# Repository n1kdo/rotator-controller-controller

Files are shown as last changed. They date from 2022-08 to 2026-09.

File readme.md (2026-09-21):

# Raspberry Pi Pico W IOT Antenna Rotator Controller Controller

This project uses a Raspberry Pi Pico W to internet-enable an antenna 
rotator controller that has an RS-232 interface.  The software presents a web interface 
to the rotator, and also allows direct network control by N1MM+ and other software.

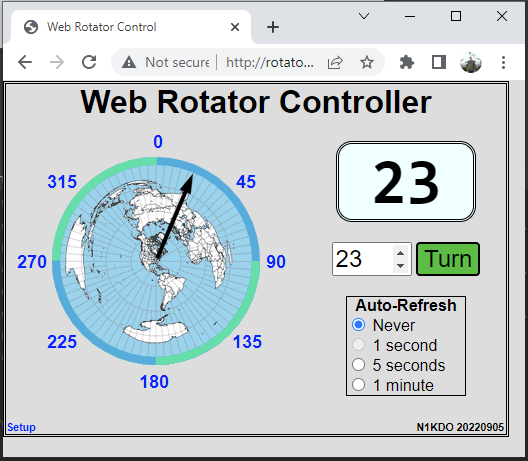
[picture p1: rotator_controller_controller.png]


I used it for my Hy-Gain Ham IV rotator.  My Hy-Gain rotator control box has been modified to allow computer
control with the addition of a Ham Supply/Idiom Press *Rotor-EZ* module.  I further modified the rotator
control box to provide +5 Volts on Pin 1 (carrier detect) of the DE-9S RS-232 interface.  This allows the 
Raspberry Pi Pico W to rob power from the rotator control box.

See the [Documentation](documentation.md) for details.

There is very little external hardware required.  The most important other piece is a MAX3232 3.3 volt 
RS-232 level converter.  The MAX3232 is used to interface the 3.3 volt logic of the Raspberry Pi Pico W to
the RS-232 levels required by the antenna rotator control box.

## Installing MicroPython on your Pico-W

1. Download the latest stable build of [Pico W MicroPython](https://micropython.org/download/RPI_PICO_W/). 
   [This is the direct link](https://www.micropython.org/resources/firmware/RPI_PICO_W-20260824-v1.29.0.uf2).
2. Connect a micro-USB cable to your PC.  Hold down the white "BOOTSEL" button on the Pico-W, and insert the
   micro-USB cable into your Pico-W.
3. The Pico-W should appear as a USB storage device on your computer.  On mine, it shows up as "RPI-RP2 (F:)".
4. Copy/Paste the MicroPython .uf2 file to this drive.
5. Disconnect the Pico-W and prepare for the next step.

## Installing this software onto the Pico-W

The easiest way to get this software installed onto your Pico-W is to use the `loader.py` tool, also
provided in this repository.

1. Download Python 3 from https://www.python.org/downloads/ and install it.  Make sure to select "Add 
   Python 3 to Path."
2. Download the contents of this GitHub repository as a zip.  Use this URL: 
   `https://github.com/n1kdo/rotator-controller-controller/archive/refs/heads/master.zip`
3. Unpack that zip file somewhere. 
4. Open a command prompt.  (your choice.  Could be PowerShell, could be good ole CMD.)
5. From the command line, execute the following command: `pip install pyserial` -- this will install the Python 
   serial port support/
6. Change directory to where you unpacked the GitHub zip file, and then
   change directory to the `src/loader` directory.
7. From the command line, execute the following command: `python loader.py` -- this will install all the rotator
   controller-controller software onto the Pico-W.

If you want to experiment, you can use the open-source "Thonny" IDE to load the python source code and HTML files
onto the Pico W.  Unfortunately, Thonny cannot load the binary file `compass-background.png` image file into the
proper location, but this can be worked around by using the "upload" feature in the controller-controller software.

## What is all this stuff?

Important files:

* src/rotator/main.py -- the main Python application
* src/rotator/dcu1_rotator.py -- a Python module that queries and commands the rotator controller
* src/rotator/http_server.py -- a Python module that implements the web server
* src/rotator/morse_code.py -- a Python module that implements the morse code sender
* src/rotator/n1mm_udp.py -- a Python module that implements UDP send/receive to/from N1MM+
* src/rotator/content/rotator.html -- the rotator control web page
* src/rotator/content/setup.html -- the setup web page
* src/rotator/content/files.html -- the file upload/download web page
* src/rotator/data/config.json -- the configuration file.  automatically generated on first use if not present.

Other Stuff:

* src/loader/loader.py -- small Python application installs the six files above onto the Pico-W
* src/loader/pyboard.py -- patched pyboard library from Micropython. Patched to work on Pico-W.

Electronic Design Files:

* kicad/* -- Kicad 6 design files for schematic and PCB.

## Other projects using this technology

I used this same electronic design, and a lot of the same source code to make
the [KPA-500 IOT Thing](https://github.com/n1kdo/KPA500-remote), a web interface and 
KPA500-remote *host* for the Elecraft KPA-500 amplifier.

## Yes it works with N1MM+

See [Using the Rotator Controller-Controller with N1MM+](N1MM.md)

n1kdo 2026-09-21

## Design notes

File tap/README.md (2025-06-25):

# Diagnostic/Development tools.

I built some tools to examine the data communications between apps and rotators while building this.

The tools are:

## line_tap.py

line_tap.py listens to serial data, both transmit and receive, using two additional serial ports.

It uses a "custom" tap to sense the transmit and receive lines on the RS-232 interface, and it sends
that data to the two ports described above.

I used this to listen in on serial traffic to and from the rotor control box (amongh other things.)

The harware tap has proven very useful for reverse-engineering serial protocols.

### Serial tap for reverse engineering

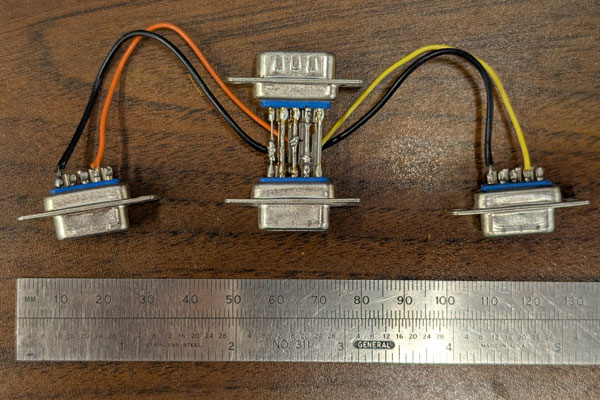
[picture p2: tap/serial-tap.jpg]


#### Serial Tap Wiring.

All pins are wired through from the device under test (DUT) _plug_ to the 
host socket.  Ground (pin 5) is wired to both the RX Tap and TX Tap grounds.  DUT TX
is wired to the TX Tap RX, and Host RX is wired to the RX Tap RX line.  The `line_tap.py`
script displays data from both paths.

| Pin | DE-9S Host | DE-9P DUT | DE-9P RX Tap | DE-9P TX Tap |
|-----|---|---|---|---|
| 1 | 1 | 1 | | |
| 2 | 2 | 2 | 2 | |
| 3 | 3 | 3 | | 2 |
| 4 | 4 | 4 | | |
| 5 | 5 | 5 | 5 | 5 |
| 6 | 6 | 6 | | |
| 7 | 7 | 7 | | |
| 8 | 8 | 8 | | |
| 9 | 9 | 9 | | |

# udp_listener.py

This script sends and receives Rotator control UDP messages to/from N1MM+

n1kdo 20250625

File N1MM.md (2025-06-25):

# Using the Rotator Controller-Controller with N1MM+

The rotator controller-controller software supports UDP messages in order that 
the connected rotator can be controlled with N1MM+.  You don't need any wires 
other than what connects the logging computer to the rotator controller-controller.

## Setup

Check the `N1MM Broadcasts` box, and make sure you have a unique `hostname` set.

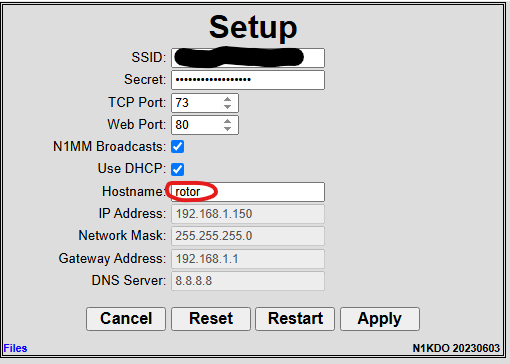
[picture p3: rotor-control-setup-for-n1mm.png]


## N1MM+ Setup

On the N1MM+ _configurator_ dialog, in the _Antennas_ tab, create an entry for an antenna,
specify the bands of that antenna, and make sure to use the _hostname_ specified above as the 
"Rotor Description."  The name must match exactly.

**Do not check** the "Start N1MM Rotor Program" -- you don't need it, you won't be using it.

Check one or both of the "Display Rotors" options.  The "...Responding from Network" option
will show all rotors that are reachable on the network; this will show you where the rotor(s)
are pointed _whether your station is using them or not._

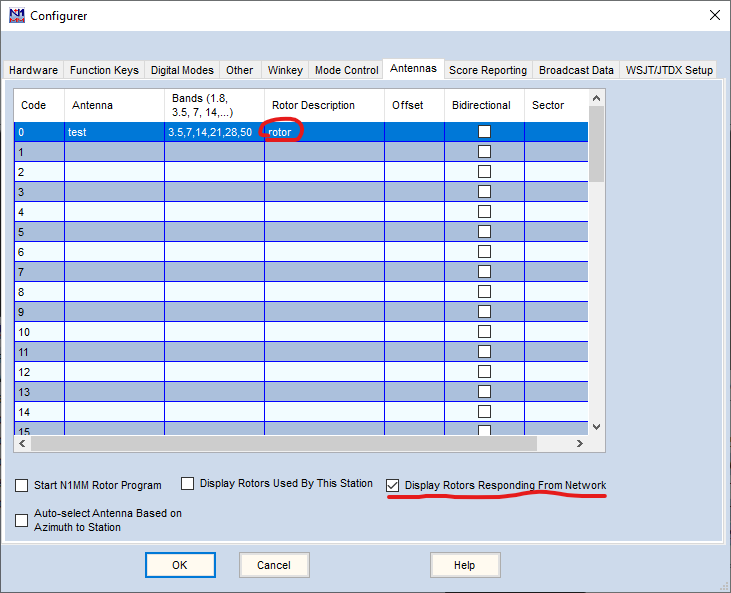
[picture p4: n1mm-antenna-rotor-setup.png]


## Operating

You should see a small window that shows the bearing of each configured rotor.  You will see the
rotor name/host name in the title bar of that window.



You can "move" the rotor by typing a bearing into the N1MM logger callsign box and pressing Alt-J.
This should turn the rotor to the new bearing.

N1MM has other tricks to turn a configured rotor; those are beyond the scope of this document.

---

n1kdo 2025-06-25

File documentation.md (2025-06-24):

# A Wireless Rotator Controller-Controller

Or: _How to Add Internet-of-Things Capabilities to Legacy Products_   
Jeff Otterson, N1KDO

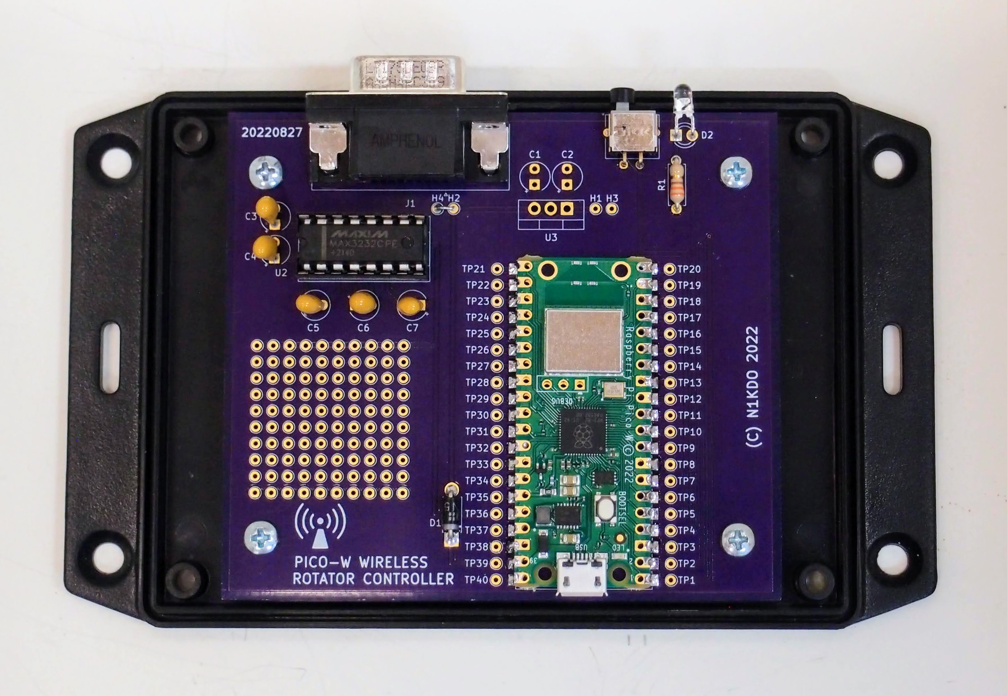
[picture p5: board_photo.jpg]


## Introduction

I live in a HOA neighborhood, which means no towers, no permanently installed visible antennas. For several years I have
been using a small 3-element Yagi which I temporarily erect on a tripod mount on my back patio for the May-August
6-meter Es season. This works well, but I have grown tired of “Armstrong”-style rotation of this antenna. I wanted to
use my Ham-IV antenna rotator to turn this antenna but did not want to go to the trouble of installing—and 
lightning-protecting the wiring for the rotator. Instead, I decided to find an approach to inexpensively add wireless 
control to the antenna rotator.

The first step was to modify the Ham-IV control box to add a computer interface. I bought the “Rotor-EZ” kit from
HamSupply (note 1) and installed it, to add RS-232 serial communications support to the Ham-IV. The Rotor-EZ uses the
same protocol as the HyGain DCU-3 and several other rotator controllers. This got me closer to my goal, but RS-232 still
needs wires!

In June 2022, the Raspberry Pi foundation announced their new “Raspberry Pi Pico-W” (note 2) – when I saw this new part,
I realized it was “just what the doctor ordered” for my project. I bought a few and started experimenting.

This article describes the results of my work: a wireless rotator controller-controller. The project connects the
rotator controller to your Wi-Fi network and allows both web-based and computer access to the rotator over wireless. The
approach I present here is useful for other Amateur Radio Internet-of-Things projects; I already have plans to use this
as a basis for wireless control of a remote antenna switch.

## How it works

If you look at the [schematic diagram](schematic.pdf), you will notice that there are very few electronic components.
Most of the components are used in the RS-232 level conversion. Like most everything else, this project is mostly in the
software.

The software can be grouped into two major parts: the “front-end” and the “back-end.” The back-end software runs on the
Pico-W and provides the web server, network serial port listener, and serial port communications to the rotator
controller. The back end is implemented in “Micro-Python,” (note 3) a version of Python that has been “optimized to run
on microcontrollers.”

The front-end software runs on your web browser and is implemented in HTML, CSS, and JavaScript. All the software is
open-source, licensed under the BSD “2-clause” license, and is available from my GitHub repository. (note 4)

The “hardware” is quite simple. The Pico-W operates at 3.3 volts, but the RS-232 interface presented by the rotator
controller operates at -12 and +12 volts (ideally). A Maxim MAX3232 IC is used to convert the voltage levels between 3.3
volts and RS-232 levels. There is also a LED and current limiting resistor, and the “mode” pushbutton.

## Construction

The basic circuit has only 10 electronic components in addition to the Pico-W. It can easily be built on perf board;
this is how I built my prototype. I laid out a circuit board that makes assembly and packaging easy. Both the schematic
and the circuit board were designed using the open-source Kicad 6 software; all the artifacts are in the GitHub
repository.

No particular care is needed in the wiring as all the signals are low speed. Attention should be given to the polarity
of the tantalum capacitors, the Schottky diode, and the LED. The LED needs the leads bent 90 degrees about 1/8 of an
inch from the body, with the shiny part of the LED facing away from you, and the longer lead on the right, carefully
bend the legs down so that the LED will slightly hang over the edge of the board.

You can mount the Pico-W directly to the circuit board. This is a bit fiddly, and there is one chance to get it right. I
suggest inserting a three-pin header through the “DEBUG” holes on the Pico-W to set the preliminary alignment. Solder
down one corner pin of the Pico-W, then inspect the alignment. Carefully re-heat that joint if you need to slightly move
the Pico-W. When you are happy with the alignment, then you can solder the other corner down, and check again. Then
solder the rest of the pins.

If you choose not to directly solder the Pico-W to the circuit board, you could mount it on headers and install sockets
onto the circuit board.

The circuit board is designed to fit into a Hammond plastic enclosure. I like Hammond because they support amateur radio
with advertising and the occasional hamfest booth. The board is meant to be mounted on the flanged lid of the enclosure;
you can either cut slots or carefully drill and cut to allow access to the DE-9 connector, mode pushbutton, and status
LED.

## Powering the circuit

There are three methods of powering the circuit. While installing the Rotor-EZ into my rotator controller, I hard-wired
+5 volts to pin 1 of the DE9 connector from the rotator controller. (This pin is normally used as “carrier detect” for a
MODEM, it is safe to put +5 here, it will not blow up any connected equipment.) Install a wire jumper from H2 to H4 on
the board to “rob” power from the rotator controller.

The circuit can also be powered through the micro-USB connector on the Pico-W and a cellphone charger can be used to
power it through this connector. When installing software, the board is powered by the host through the USB connection.

Finally, to support further experimentation, the board has provisions to allow the installation of a 7805 voltage
regulator and associated bypass capacitors. Unregulated voltage is supplied on H1, and ground is on H3.

## The Playground

I knew I had other ideas for this project, I added a 10x10 grid of solder pads to the board for future experimentation.
The top row of pins is wired to +3.3 volts, and the bottom row of pins to ground. In addition, every pin of the Pico-W
is brought out to a “test point” hole, so the signals are easy to access.

## Installing the Software

There are two phases to installing the software on the device. The first phase is to install MicroPython and the second
is to install the controller-controller software. Instructions for both operations are in the GitHub repository.

## Using the Controller-Controller

The controller-controller web interface provides three different functions: rotator operation, configuration, and
customization. Each is described below.

## Operating Mode

  
Figure 1: Rotator Controller-Controller operating page

The primary operating mode allows rotation of the antenna. Figure 1 shows this page. This web page shows the current
bearing of the antenna, provides quick links for eight different directions, and allows the bearing to be entered. The
direction indicator arrow will move as the rotator turns. In addition, the bearing indicator can be set up to
automatically update periodically, which is useful if the rotator is being commanded from more than one location.

## Setup Mode

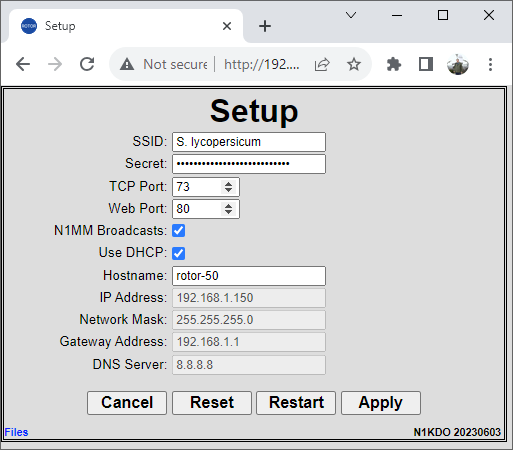
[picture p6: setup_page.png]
  
Figure 2: Setup Page

Figure 2 shows the “setup” page for the controller-controller. This page allows you to configure the SSID and secret
used to connect to your Wi-Fi network and allows the TCP port number for the web interface and network serial
connection. You can access this page by clicking the “Setup” link in the lower left corner of the operating mode page.

## Files Upload

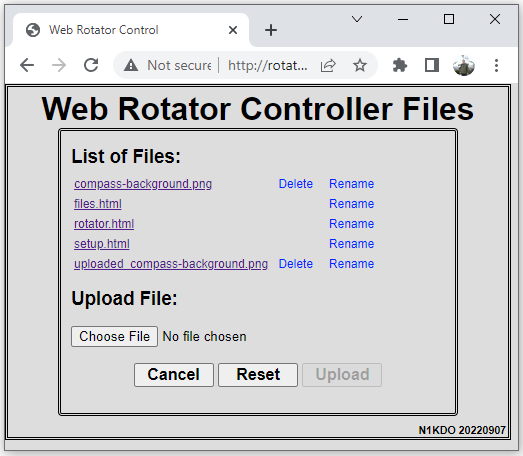
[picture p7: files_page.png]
  
FIgure 3: Files page

Figure 3 shows the “Files” page for the controller-controller. This page allows you to customize the look and feel of
the device by modifying the HTML and other assets. This can be dangerous since these HTML files provide the look and
feel of the web interface. The existing implementation of this page does not allow the deletion of any .html file and
renames every uploaded file with the prefix “uploaded_” in order to prevent disaster. You can upload new files and test
them prior to deleting existing files and renaming the uploaded files. Extreme care should be taken if you choose to
modify “files.html” – if you damage the functionality provided here, you will need to find another way to re-install a
working version. Be careful!

## Network Serial Port Operation

While a web interface to your rotator controller is certainly useful, the project also allows computer control of the
rotator through network serial port emulation. This allows your logging or contesting software to command the rotator
over the network. If your software does not support network serial port access (most does not) then you can use software
like ‘com0com’ and ‘com2tcp’ (note 5) to create a “virtual” serial port on your PC that connects to the rotator
controller-controller through the network. I have verified that this works by testing with both “LP-Rotor”  (note 6) and
“DXView” (note 70. Consult your favorite search engine for com0com and com2tcp set up information.

## N1MM+ Integration

The rotator controller-controller can also interoperate with N1MM+. It accepts and transmits UDP network messages that
allow the rotator to be directly controlled over the network with N1MM+.

## Chickens and Eggs

The controller-controller has a setup web page that allows you to set the SSID and secret to connect to you Wi-Fi
network, but how can you access this page if the controller is not already connected to your network? This is the
function of the “mode” button. When the mode button is pressed, the controller-controller restarts as a Wi-Fi access
point named “Rotator” with the secret password “NorthSouth”. Connect to this access point with your phone or other Wi-Fi
device. Some devices will complain that this network does not offer Internet access--that is ok, because it does not!
You may need to check a box to keep your device connected to this network.

Once connected to the “Rotator” network, use your web browser to access the controller-controller by loading the web
page at http://192.168.4.1 – from here you can click the “Setup” link and configure the controller-controller. After you
enter your network’s SSID and secret, click the “Apply” button to save the configuration, and then press the “Restart”
button to return the controller-controller to normal mode.

Access point mode can also be used in locations where there is no Wi-Fi service, the controller-controller is completely
usable in access point mode.

## A note about IP addressing

The controller-controller blinks out its current IP address on the LED in Morse code. The code speed is slow enough that
you can copy it by pencil, writing down the dits and dahs and later translating by hand if that is needed. When in
access point mode, the IP address is prefixed with the letters “AP” to indicate this mode. If it cannot connect to your
network, it will blink out “0 0 0 0” – this is an error condition, and you will need to use the mode button to select
access point mode to retry the configuration.

If your network router supports the feature, I recommend using “static DHCP” so that the controller-controller will
always receive the same IP address. The board may appear on your router as a device named “PYBD”. Consult your router’s
documentation for instructions to set up static DHCP.

## The Compass Background

One file you might see on the Files page is named “compass-background.png”. This file can be used to draw a “great
circle” map behind the bearing indicator. The file is a 200x200 “png” image with a transparent background, which
contains a 200-pixel diameter great circle map. The version supplied with the project has the great circle centered at
Atlanta, Georgia. I created this map from results obtained from NS6T’s “Request an Azimuthal Map” (note 8), and a little
bit of effort in an image editor to resize and adjust.

## Warning

There is no HTTPS/TLS (network encryption) in this project, for a variety of reasons, notably the effort and complexity
needed to set up new SSL certificates. All network traffic is in the clear. Therefore, this device should not be
connected to the public Internet. Your home Wi-Fi network is fine, but I do not recommend “port-forwarding” to allow
outside access. If this is needed, you should investigate other methods of remote access, possibly using a VPN.

Also, there is no authentication needed to turn the antenna. No usernames or passwords are used. Anybody on your network
can access the rotator controller-controller.

## Happy Hacking!

It is my hope that this project will be useful by itself, but also serve as a base for experimenters to create their own
IOT integrations with their existing gear. The Pico-W represents a tremendous opportunity to build this kind of stuff on
the cheap. I hope you find this project useful and interesting.

## Parts List

```
C1-C7 .1 uF 35V tantalum capacitor, KEMET T350A104M035AT or similar, see notes
D1 1N5819 40V 1A Schottky Diode
D2 T1 White LED, LITEON LTW-420D7 or similar
J1 DE9P connector, Amphenol L717SDE09PA4CH4RC309
R1 330 ohm ¼ watt leaded resistor
SW1 SPST-NO pushbutton, NKK Switches GB215AH
SW1-cap pushbutton cap NKK Switches AT4063A
U1 Raspberry Pi Pico-W, see notes 
U2 MAX3232 16-pin DIP MAXIM MAX3232ECPE+
U3 7805 three-terminal 5V regulator in TO-220 case, TI UA7805CKCT or similar, see notes
Enclosure: Hammond 1591XXSFLBK
```

### Notes:

If you decide to include the 5 volt regulator parts, include C1, C2, and C3, otherwise, these are not needed.

The Raspberry Pi Pico-W is in short supply. I have bought some from Vilros.com, SparkFun.com, and CanaKit.com (from
Canada). Adafruit.com also lists them. They are inexpensive enough, and so much fun, that I will usually buy two when I
find availability.

## References

1. "Rotor-EZ for Hy-Gain Rotator Control," HamSupply.com, 2022. [Online].
   Available: https://www.hamsupply.com/rotor-ez-hy-gain-rotor-control/.
2. E. Upton, "Raspberry Pi Pico W: your $6 IoT platform," Raspberry Pi Foundation, 30 June 2022. [Online].
   Available: https://www.raspberrypi.com/news/raspberry-pi-pico-w-your-6-iot-platform/.
3. D. George, "MicroPython," George Robotics, 2018. [Online]. Available: https://micropython.org/.
4. J. Otterson, "rotator-controller-controller," N1KDO, 17 September 2022. [Online].
   Available: https://github.com/n1kdo/rotator-controller-controller.
5. vfrolov, "Null-modem emulator," Sourceforge.com, 09 April 2018. [Online].
   Available: https://sourceforge.net/projects/com0com/.
6. L. Phipps, "http://www.telepostinc.com/LP-Rotor-Html/," Telepost, Inc, 2003. [Online].
   Available: http://www.telepostinc.com/LP-Rotor-Html/.
7. D. Bernstein, "DXView," AA6YQ, 20 April 2022. [Online]. Available: https://www.dxlabsuite.com/dxview/.
8. T. Epperly, "Request an Azimuthal Map," NS6T, 2013. [Online]. Available: https://ns6t.net/azimuth/azimuth.html.

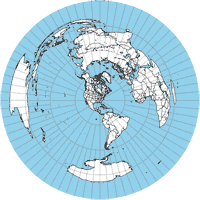
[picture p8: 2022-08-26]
src/rotator/content/compass-background.png

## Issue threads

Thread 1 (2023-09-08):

gps intigration

Aquahoodjd, 2023-09-08:
what go you thing about a low cost gps multi format chip with a ceramic gap anttena or you ould add your own qhf helix (these rock by the way. You could orient your rotator of various design north to calibrate with gps, g predict, the messier catalog for astrophoto with a cam mount added?

Aquahoodjd, 2023-09-08:
excuse the spelling

n1kdo, 2023-09-18:
Hi,  this project controls an antenna rotator control box, not the rotator directly, so I am not sure your issue is applicable.  Thanks for looking, anyhow.  Jeff

Closed 2023-09-18.

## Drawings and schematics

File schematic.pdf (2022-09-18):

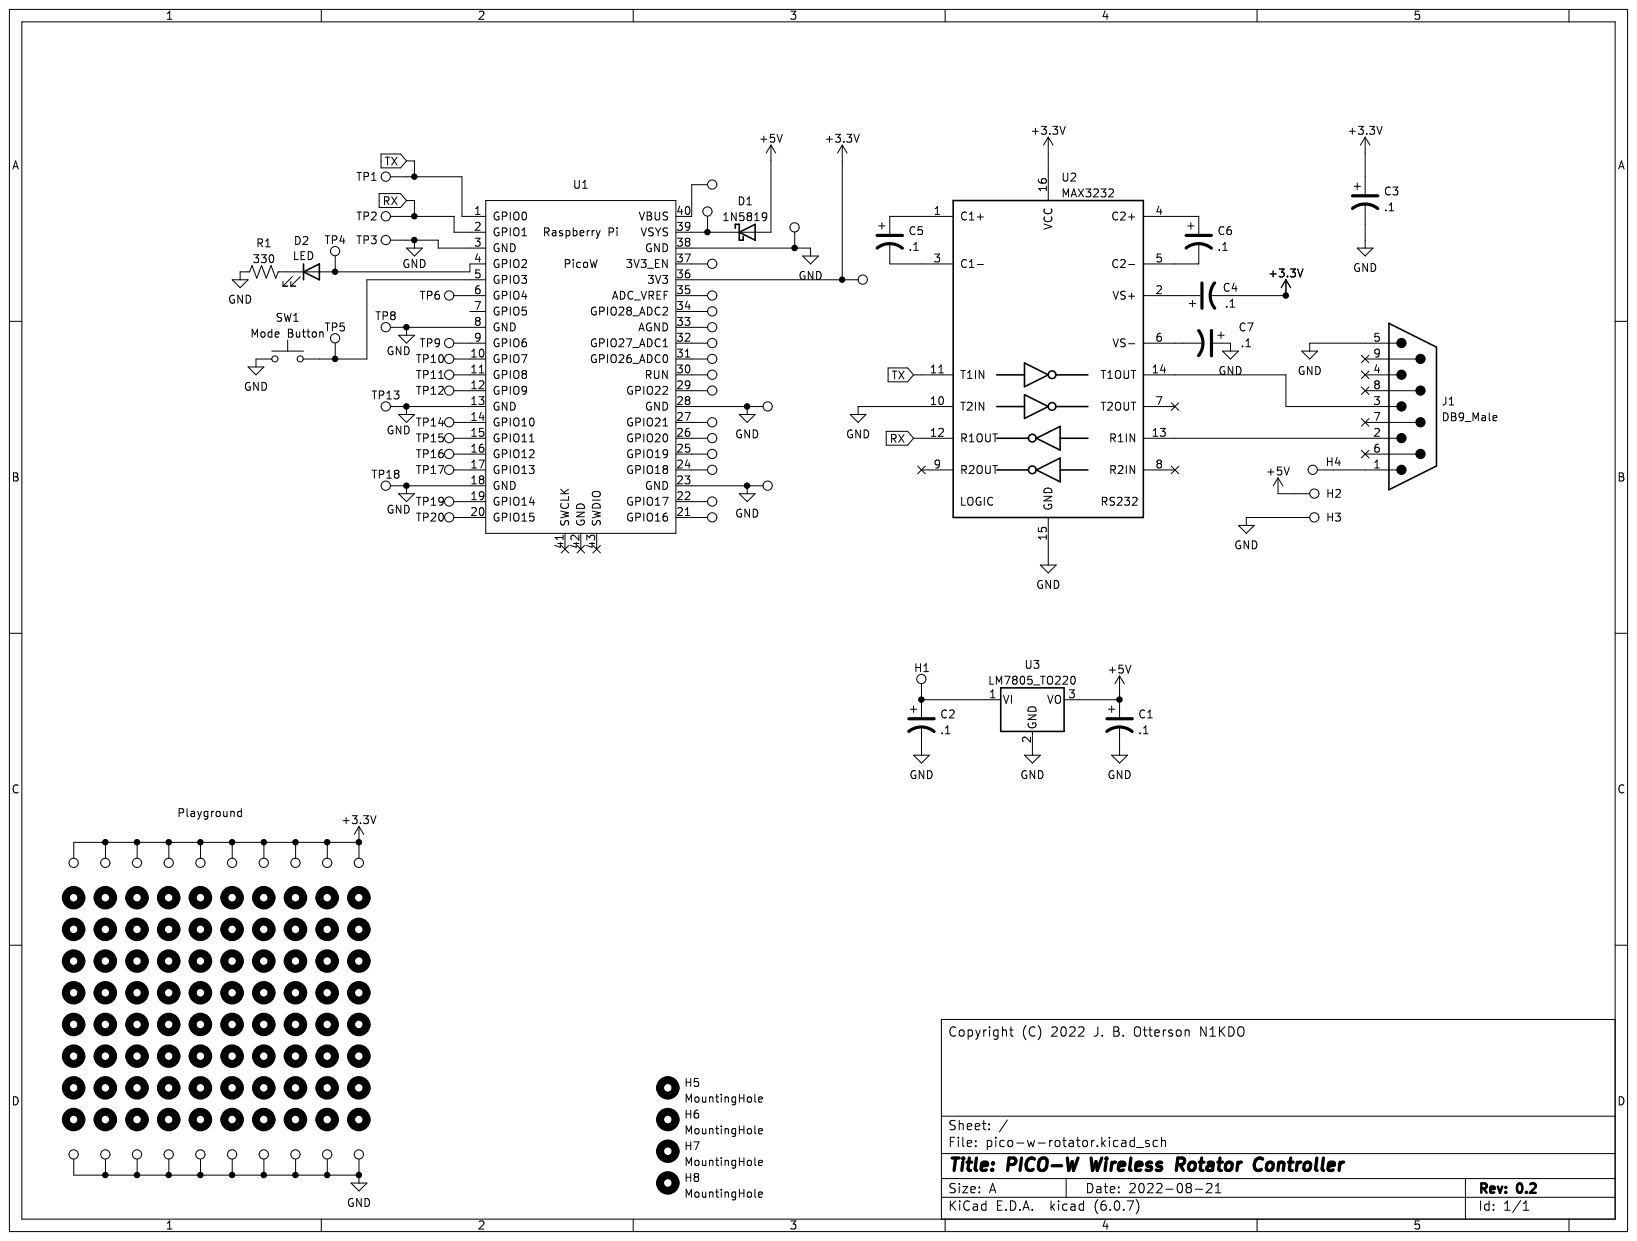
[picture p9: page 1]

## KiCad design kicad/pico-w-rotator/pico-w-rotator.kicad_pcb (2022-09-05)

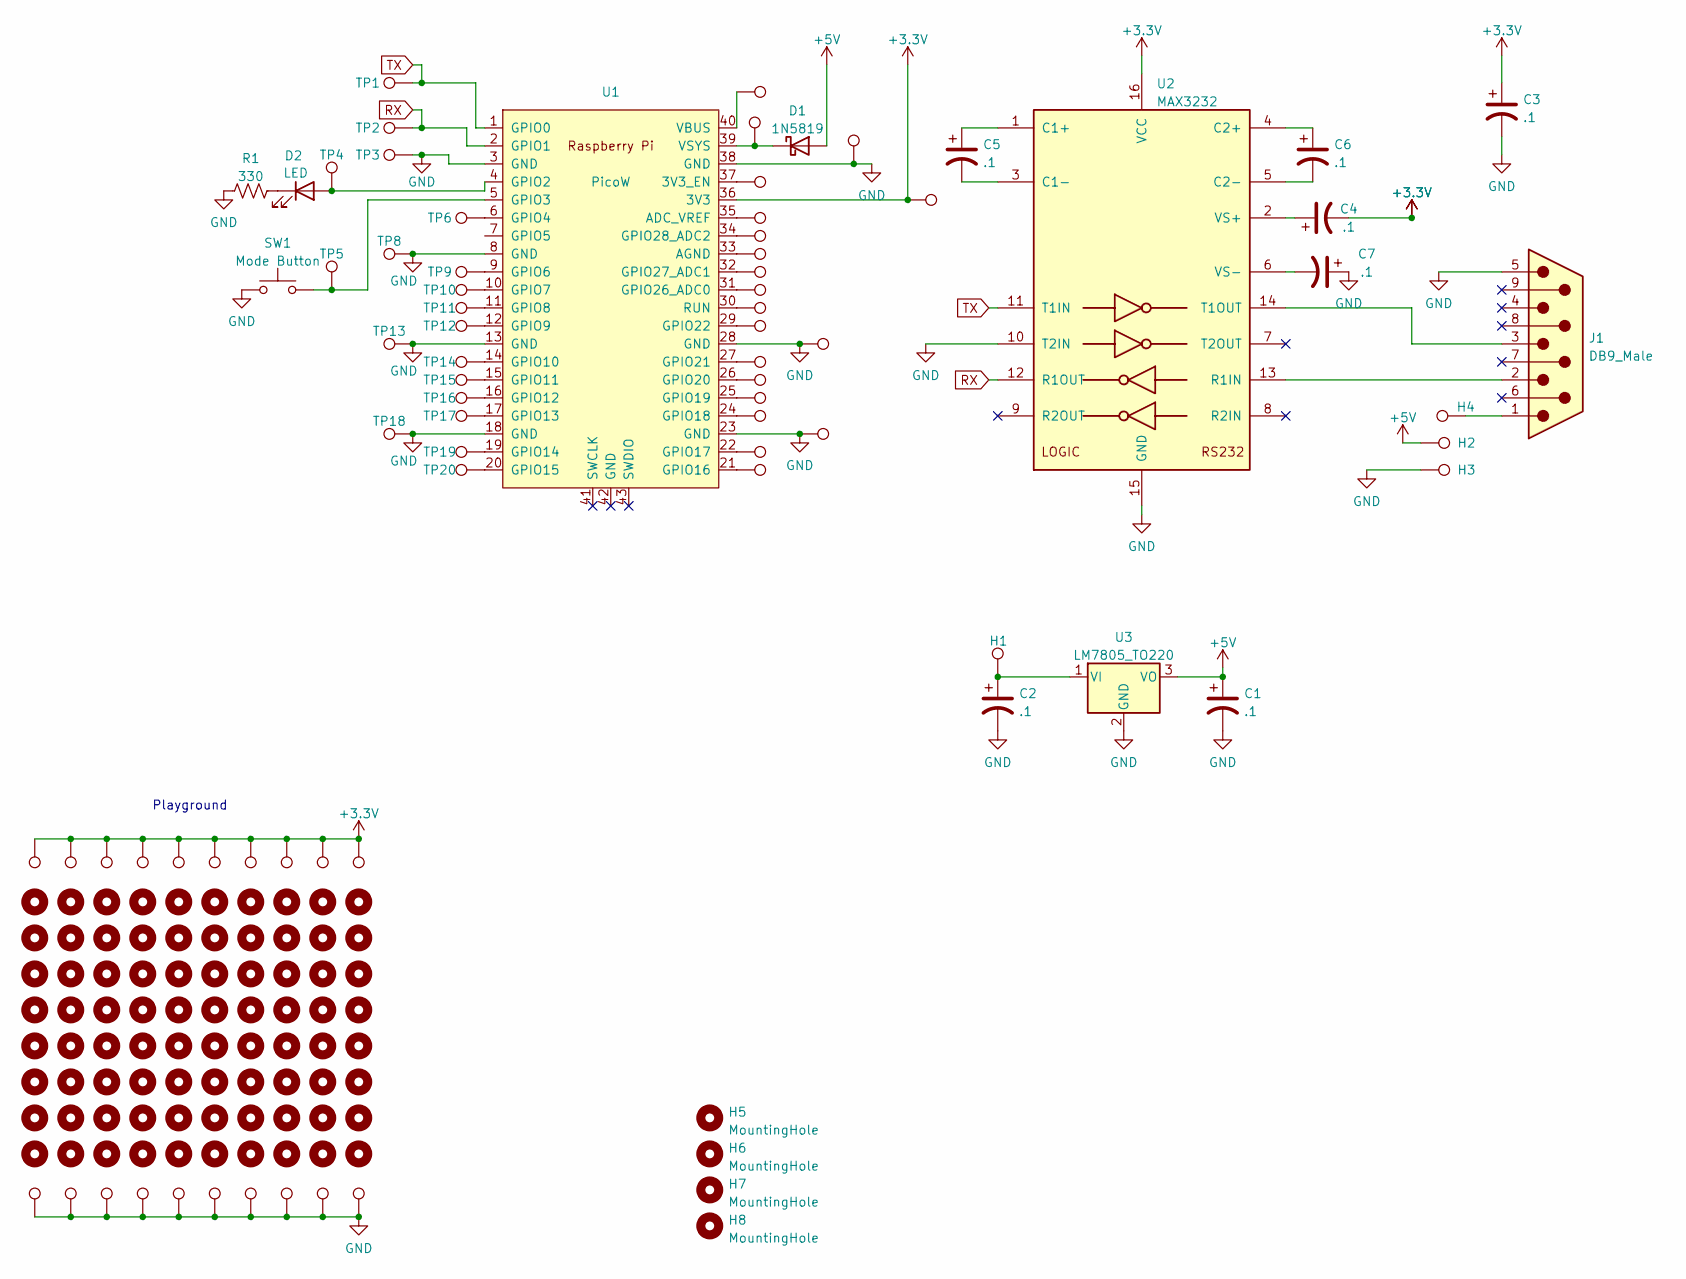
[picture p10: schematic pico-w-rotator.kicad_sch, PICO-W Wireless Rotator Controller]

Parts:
C1, C2, C3, C4, C5, C6, C7: .1; CP_Radial_Tantal_D4.5mm_P2.50mm; part T350A104M035AT
D1: 1N5819; D_DO-41_SOD81_P7.62mm_Horizontal
D2: LED; LED_D3.0mm
GH1, GH2, GH3, GH4, GH5, GH6, GH7, GH8, GH9, GH10, GH11, GH12, GH13, GH14, GH15, GH16, GH17, GH18, GH19, GH20, GH21, GH22, GH23, GH24, GH25, GH26, GH27, GH28, GH29, GH30, GH31, GH32, GH33, GH34, GH35, GH36, GH37, GH38, GH39, GH40, GH41, GH42, GH43, GH44, GH45, GH46, GH47, GH48, GH49, GH50, GH51, GH52, GH53, GH54, GH55, GH56, GH57, GH58, GH59, GH60, GH61, GH62, GH63, GH64, GH65, GH66, GH67, GH68, GH69, GH70, GH71, GH72, GH73, GH74, GH75, GH76, GH77, GH78, GH79, GH80, GH81, GH82, GH83, GH84, GH85, GH86, GH87, GH88, GH89, GH90, GH91, GH92, GH93, GH94, GH95, GH96, GH97, GH98, GH99, GH100: MountingHole; TestPoint_THTPad_D1.0mm_Drill0.5mm
H1, H3: 3; TestPoint_THTPad_D1.0mm_Drill0.5mm
H2: 2; TestPoint_THTPad_D1.0mm_Drill0.5mm
H4: 1; TestPoint_THTPad_D1.0mm_Drill0.5mm
H5, H6, H7, H8: MountingHole; MountingHole_3.5mm
J1: DB9_Male; DSUB-9_Male_Horizontal_P2.77x2.84mm_EdgePinOffset4.94mm_Hou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; part L717SDE09PA4CH4RC309
R1: 330; R_Axial_DIN0207_L6.3mm_D2.5mm_P7.62mm_Horizontal
SW1: Mode Button; GB215AHB; part GB215AH
TP1, TP2, TP3, TP4, TP5, TP6, TP8, TP9, TP10, TP11, TP12, TP13, TP14, TP15, TP16, TP17, TP18, TP19, TP20, TP21, TP22, TP23, TP24, TP25, TP26, TP27, TP28, TP29, TP30, TP31, TP32, TP33, TP34, TP35, TP36, TP37, TP38, TP39, TP40: TestPoint; TestPoint_THTPad_D1.0mm_Drill0.5mm
U1: PicoW; RPi_PicoW_SMD_TH
U2: MAX3232; DIP-16_W7.62mm_Socket
U3: LM7805_TO220; TO-220-3_Vertical

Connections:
+3.3V: C3.1, C4.2, GH1.1, GH11.1, GH21.1, GH31.1, GH41.1, GH51.1, GH61.1, GH71.1, GH81.1, GH91.1, TP36.1, U1.36 (3V3), U2.16 (VCC)
+5V: C1.1, D1.2 (A), H2.1, U3.3 (VO)
GND: C1.2, C2.2, C3.2, C7.1, GH10.1, GH20.1, GH30.1, GH40.1, GH50.1, GH60.1, GH70.1, GH80.1, GH90.1, GH100.1, H3.1, J1.5, R1.1, SW1.1, TP3.1, TP8.1, TP13.1, TP18.1, TP23.1, TP28.1, TP38.1, U1.3 (GND), U1.8 (GND), U1.13 (GND), U1.18 (GND), U1.23 (GND), U1.28 (GND), U1.38 (GND), U2.10 (T2IN), U2.15 (GND), U3.2 (GND)
unnamed: C2.1, H1.1, U3.1 (VI)
unnamed: C4.1, U2.2 (VS+)
unnamed: C5.1, U2.1 (C1+)
unnamed: C5.2, U2.3 (C1-)
unnamed: C6.1, U2.4 (C2+)
unnamed: C6.2, U2.5 (C2-)
unnamed: C7.2, U2.6 (VS-)
unnamed: D1.1 (K), TP39.1, U1.39 (VSYS)
unnamed: D2.1 (K), R1.2
unnamed: D2.2 (A), TP4.1, U1.4 (GPIO2)
unnamed: H4.1, J1.1
unnamed: J1.2, U2.13 (R1IN)
unnamed: J1.3, U2.14 (T1OUT)
unnamed: SW1.2, TP5.1, U1.5 (GPIO3)
unnamed: TP6.1, U1.6 (GPIO4)
unnamed 18: U1.7 (GPIO5); also elsewhere on the board
unnamed: TP9.1, U1.9 (GPIO6)
unnamed: TP10.1, U1.10 (GPIO7)
unnamed: TP11.1, U1.11 (GPIO8)
unnamed: TP12.1, U1.12 (GPIO9)
unnamed: TP14.1, U1.14 (GPIO10)
unnamed: TP15.1, U1.15 (GPIO11)
unnamed: TP16.1, U1.16 (GPIO12)
unnamed: TP17.1, U1.17 (GPIO13)
unnamed: TP19.1, U1.19 (GPIO14)
unnamed: TP20.1, U1.20 (GPIO15)
unnamed: TP21.1, U1.21 (GPIO16)
unnamed: TP22.1, U1.22 (GPIO17)
unnamed: TP24.1, U1.24 (GPIO18)
unnamed: TP25.1, U1.25 (GPIO19)
unnamed: TP26.1, U1.26 (GPIO20)
unnamed: TP27.1, U1.27 (GPIO21)
unnamed: TP29.1, U1.29 (GPIO22)
unnamed: TP30.1, U1.30 (RUN)
unnamed: TP31.1, U1.31 (GPIO26_ADC0)
unnamed: TP32.1, U1.32 (GPIO27_ADC1)
unnamed: TP33.1, U1.33 (AGND)
unnamed: TP34.1, U1.34 (GPIO28_ADC2)
unnamed: TP35.1, U1.35 (ADC_VREF)
unnamed: TP37.1, U1.37 (3V3_EN)
unnamed: TP40.1, U1.40 (VBUS)
RX: TP2.1, U1.2 (GPIO1), U2.12 (R1OUT)
TX: TP1.1, U1.1 (GPIO0), U2.11 (T1IN)

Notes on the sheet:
Playground

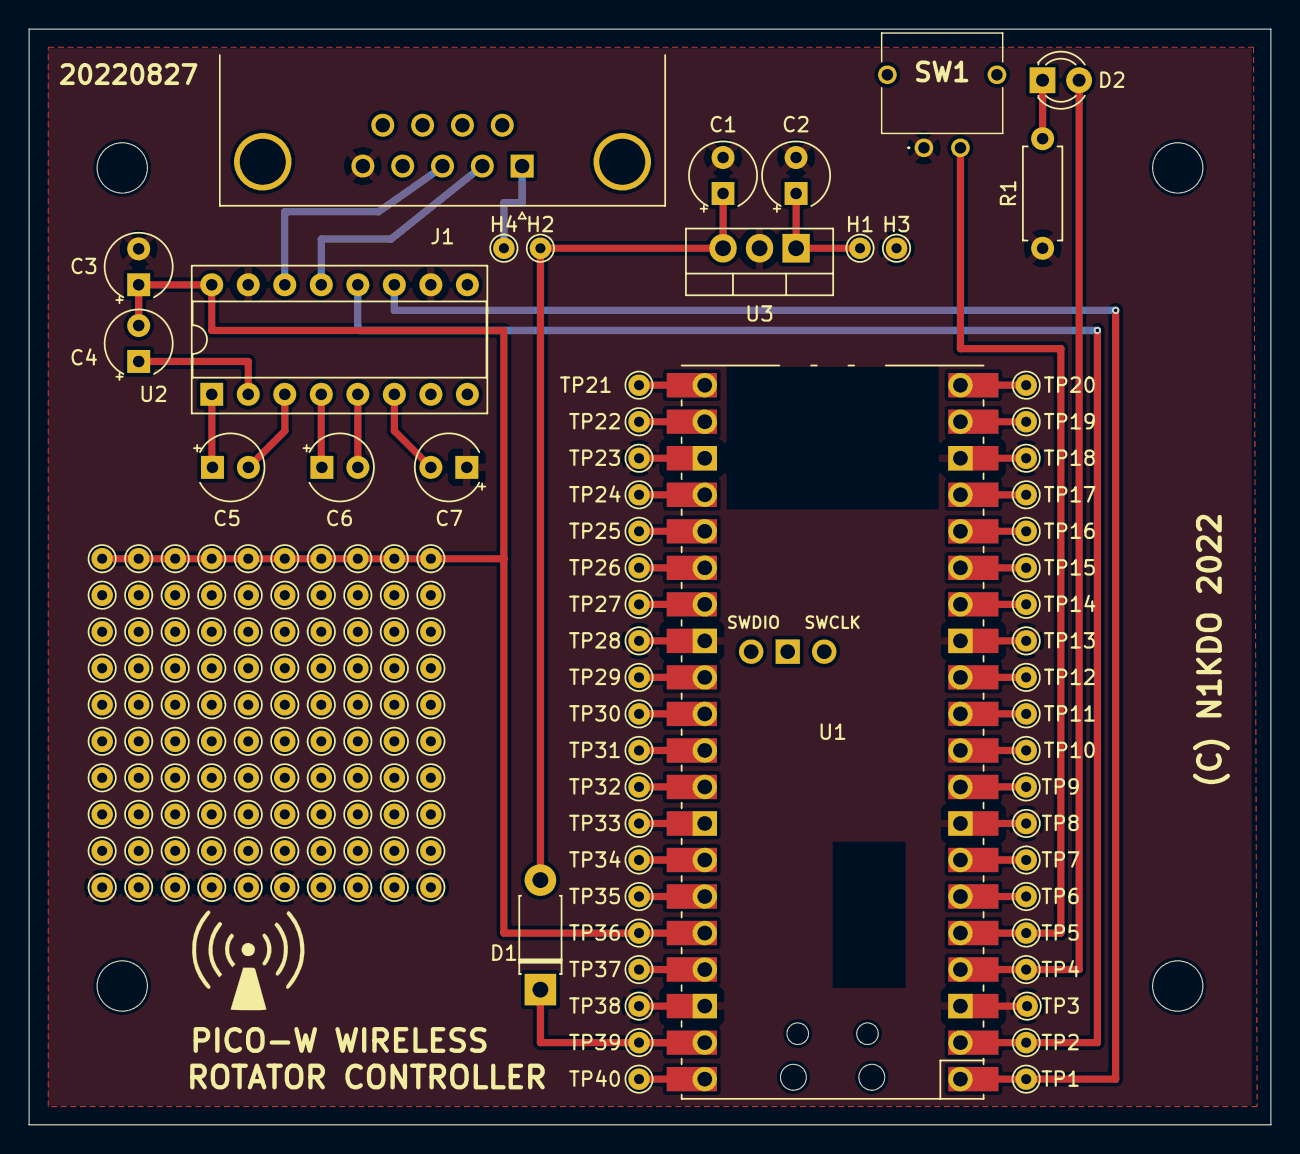
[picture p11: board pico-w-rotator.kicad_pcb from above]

Board: 2 copper layers, 86.4 x 76.2 mm, 164 parts (0 on the bottom side), 46 nets.

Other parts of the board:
G1: LOGO; non-ionizing-bigger
TP7: TestPoint; TestPoint_THTPad_D1.5mm_Drill0.7mm

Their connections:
unnamed 18: TP7.1; also elsewhere on the board

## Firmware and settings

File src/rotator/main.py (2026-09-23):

#
# main.py -- this is the web server for the Raspberry Pi Pico W Web Rotator Controller.
#

__author__ = 'J. B. Otterson'
__copyright__ = """
Copyright 2022, 2025, 2026 J. B. Otterson N1KDO.
Redistribution and use in source and binary forms, with or without modification, 
are permitted provided that the following conditions are met:
  1. Redistributions of source code must retain the above copyright notice, 
     this list of conditions and the following disclaimer.
  2. Redistributions in binary form must reproduce the above copyright notice, 
     this list of conditions and the following disclaimer in the documentation 
     and/or other materials provided with the distribution.
THIS SOFTWARE IS PROVIDED BY THE COPYRIGHT HOLDERS AND CONTRIBUTORS "AS IS" AND 
ANY EXPRESS OR IMPLIED WARRANTIES, INCLUDING, BUT NOT LIMITED TO, THE IMPLIED
WARRANTIES OF MERCHANTABILITY AND FITNESS FOR A PARTICULAR PURPOSE ARE DISCLAIMED.
IN NO EVENT SHALL THE COPYRIGHT HOLDER OR CONTRIBUTORS BE LIABLE FOR ANY DIRECT,
INDIRECT, INCIDENTAL, SPECIAL, EXEMPLARY, OR CONSEQUENTIAL DAMAGES (INCLUDING,
BUT NOT LIMITED TO, PROCUREMENT OF SUBSTITUTE GOODS OR SERVICES; LOSS OF USE, 
DATA, OR PROFITS; OR BUSINESS INTERRUPTION) HOWEVER CAUSED AND ON ANY THEORY OF
LIABILITY, WHETHER IN CONTRACT, STRICT LIABILITY, OR TORT (INCLUDING NEGLIGENCE 
OR OTHERWISE) ARISING IN ANY WAY OUT OF THE USE OF THIS SOFTWARE, EVEN IF ADVISED
OF THE POSSIBILITY OF SUCH DAMAGE.
"""
__version__ = '0.2.4'  # 2026-09-23

import asyncio
import gc
import socket

import micro_logging as logging
from dcu1_rotator import Rotator
from http_server import (HttpServer,
                         HTTP_STATUS_OK, HTTP_STATUS_BAD_REQUEST, HTTP_STATUS_MOVED_PERMANENTLY,
                         HTTP_STATUS_INTERNAL_SERVER_ERROR, HTTP_VERB_GET, HTTP_VERB_POST)
from morse_code import MorseCode
from n1mm_rotator_udp import RotatorData, calculate_broadcast_address, ReceiveBroadcastsFromN1MM, SendBroadcastsToN1MM
from utils import elapsed_ms, is_ipv4, milliseconds, safe_int, upython

if upython:
    # disable pylint import error
    # pylint: disable=E0401
    from picow_network import PicowNetwork
    import machine
else:
    from not_machine import machine

# noinspection PyUnboundLocalVariable
onboard = machine.Pin('LED', machine.Pin.OUT, value=0)
onboard.on()
morse_led = machine.Pin(2, machine.Pin.OUT, value=0)  # status LED
ap_mode_button = machine.Pin(3, machine.Pin.IN, machine.Pin.PULL_UP)

CONTENT_DIR = 'content/'

N1MM_ROTOR_BROADCAST_PORT = 12040
N1MM_BROADCAST_FROM_ROTOR_PORT = 13010

from config_data import (ConfigData,
                         DEFAULT_SSID, DEFAULT_SECRET, DEFAULT_WEB_PORT,
                         DEFAULT_TCP_PORT_1, DEFAULT_TCP_PORT_2)

# globals
keep_running = True
rotator_1 = None
rotator_2 = None

# picow_network
picow_network = None

# config data
config = ConfigData()

# http server
http_server = HttpServer(content_dir=CONTENT_DIR)


class RotatorTelnetServer:
    def __init__(self, rotator):
        self._rotator = rotator

    async def serve_serial_client(self, reader, writer):
        """
        this provides serial compatible control.
        use com0com with com2tcp to interface legacy apps on Windows.

        this code provides a serial endpoint that implements part of the DCU-3 protocol.

        all commands start with 'A'
        all commands end with ';' or CR (ascii 13)
        """
        requested = -1
        t0 = milliseconds()
        partner = writer.get_extra_info('peername')[0]
        logging.info(b'serial client connected from %s' % partner, 'main:connect_to_network')
        buffer = []

        try:
            while True:
                data = await reader.read(1)
                if not data:
                    break
                else:
                    if len(data) == 1:
                        b = data[0]
                        if b == ord('A'):  # commands always start with A, so reset the buffer.
                            buffer = [b]
                        else:
                            if len(buffer) < 8:  # anti-gibberish test
                                buffer.append(b)
                                if b == ord(';') or b == 13:  # command terminator
                                    command = bytes(buffer)
                                    buffer = []  # discard the completed command
                                    if command in (b'AI1;', b'AI1\r'):  # get direction
                                        bearing = await self._rotator.get_rotator_bearing()
                                        writer.write(b';%03d' % bearing)
                                        await writer.drain()
                                    elif command.startswith(b'AP1') and command[-1] == 13:  # set + move
                                        requested = safe_int(command[3:-1], -1)
                                        if 0 <= requested <= 360:
                                            await self._rotator.set_rotator_bearing(requested)
                                    elif command.startswith(b'AP1') and command[-1] == ord(';'):  # set bearing
                                        requested = safe_int(command[3:-1], -1)
                                    elif command == b'AM1;' and 0 <= requested <= 360:  # move rotator
                                        await self._rotator.set_rotator_bearing(requested)
        except Exception as exc:
            logging.exception('exception in serve_serial_client:', 'RotatorTelnetServer:serve_serial_client',
                              exc_info=exc)
        finally:
            try:
                writer.close()
                await writer.wait_closed()
            except Exception as exc:
                logging.exception('exception closing serial client:', 'RotatorTelnetServer:serve_serial_client',
                                  exc_info=exc)
            gc.collect()
        logging.info(b'serial client disconnected, elapsed time %6.3f seconds' % (elapsed_ms(t0) / 1000.0),
                     'RotatorTelnetServer:serve_serial_client')


# noinspection PyUnusedLocal
@http_server.route(b'/')
async def slash_callback(http, verb, args, reader, writer, request_headers=None):  # callback for '/'
    http_status = HTTP_STATUS_MOVED_PERMANENTLY
    bytes_sent = await http.send_simple_response(writer, http_status, None, None, [b'Location: /rotator.html'])
    return bytes_sent, http_status


# noinspection PyUnusedLocal
@http_server.route(b'/api/config')
async def api_config_callback(http, verb, args, reader, writer, request_headers=None):  # callback for '/api/config'
    if verb == HTTP_VERB_GET:
        payload = config.get_data().copy()
        payload.pop('secret')  # do not return the secret in the api response.
        http_status = HTTP_STATUS_OK
        bytes_sent = await http.send_simple_response(writer, http_status, http.CT_APP_JSON, payload)
    elif verb == HTTP_VERB_POST:
        errors = []
        new_values = {}
        tcp_port_1 = safe_int(args.get('tcp_port_1'), -2)
        tcp_port_2 = safe_int(args.get('tcp_port_2'), -2)
        web_port = safe_int(args.get('web_port'), -2)
        if 0 <= tcp_port_1 <= 65535:
            new_values['tcp_port_1'] = tcp_port_1
        else:
            errors.append(b'tcp_port_1')
        if 0 <= tcp_port_2 <= 65535:
            new_values['tcp_port_2'] = tcp_port_2
        else:
            errors.append(b'tcp_port_2')
        # a web port of zero is not permitted; the web interface must always be available.
        if 1 <= web_port <= 65535:
            new_values['web_port'] = web_port
        else:
            errors.append(b'web_port')
        # a port of zero means that rotor's tcp service is disabled; it cannot collide with anything.
        # ports not in this POST keep their currently-configured values for collision checking.
        effective_tcp_port_1 = tcp_port_1 if 1 <= tcp_port_1 <= 65535 else safe_int(config.get('tcp_port_1'), -1)
        effective_tcp_port_2 = tcp_port_2 if 1 <= tcp_port_2 <= 65535 else safe_int(config.get('tcp_port_2'), -1)
        effective_web_port = web_port if 1 <= web_port <= 65535 else \
            safe_int(config.get('web_port') or DEFAULT_WEB_PORT, DEFAULT_WEB_PORT)
        if not 1 <= effective_tcp_port_1 <= 65535:
            effective_tcp_port_1 = None
        if not 1 <= effective_tcp_port_2 <= 65535:
            effective_tcp_port_2 = None
        if effective_tcp_port_1 is not None and effective_tcp_port_1 == effective_web_port:
            errors.append(b'tcp_port_1 (collides with web_port)')
        if effective_tcp_port_2 is not None and \
                effective_tcp_port_2 in (effective_tcp_port_1, effective_web_port):
            errors.append(b'tcp_port_2 (collides with tcp_port_1 or web_port)')
        ssid = args.get('SSID')
        if ssid is not None:
            if 0 < len(ssid) <= 32:
                new_values['SSID'] = ssid
            else:
                errors.append(b'SSID')
        secret = args.get('secret')
        if secret is not None and len(secret) != 0:
            if 8 <= len(secret) <= 63:
                new_values['secret'] = secret
            else:
                errors.append(b'secret')
        n1mm_arg = args.get('n1mm')
        if n1mm_arg is not None:
            n1mm = n1mm_arg == 1
            new_values['n1mm'] = n1mm
        dhcp_arg = args.get('dhcp')
        if dhcp_arg is not None:
            dhcp = dhcp_arg == 1
            new_values['dhcp'] = dhcp
        hostname_arg = args.get('hostname')
        if hostname_arg is not None:
            if 0 < len(hostname_arg) <= 16:
                new_values['hostname'] = hostname_arg
            else:
                errors.append(b'hostname')
        rotor_1_name = args.get('rotor_1_name')
        if rotor_1_name is not None:
            if isinstance(rotor_1_name, str) and 1 <= len(rotor_1_name) <= 16 and \
                    not any(ch in ' \t\r\n\f' for ch in rotor_1_name):
                new_values['rotor_1_name'] = rotor_1_name
            else:
                errors.append(b'rotor_1_name')
        rotor_1_primitive = args.get('rotor_1_primitive')
        if rotor_1_primitive is not None:
            new_values['rotor_1_primitive'] = rotor_1_primitive == 1
        rotor_2_name = args.get('rotor_2_name')
        if rotor_2_name is not None:
            # an empty name is permitted here, it indicates no second rotor.
            if isinstance(rotor_2_name, str) and len(rotor_2_name) <= 16 and \
                    not any(ch in ' \t\r\n\f' for ch in rotor_2_name):
                new_values['rotor_2_name'] = rotor_2_name
            else:
                errors.append(b'rotor_2_name')
        rotor_2_primitive = args.get('rotor_2_primitive')
        if rotor_2_primitive is not None:
            new_values['rotor_2_primitive'] = rotor_2_primitive == 1
        ip_address = args.get('ip_address')
        if ip_address is not None:
            if is_ipv4(ip_address):
                new_values['ip_address'] = ip_address
            else:
                errors.append(b'ip_address')
        netmask = args.get('netmask')
        if netmask is not None:
            if is_ipv4(netmask):
                new_values['netmask'] = netmask
            else:
                errors.append(b'netmask')
        gateway = args.get('gateway')
        if gateway is not None:
            if is_ipv4(gateway):
                new_values['gateway'] = gateway
            else:
                errors.append(b'gateway')
        dns_server = args.get('dns_server')
        if dns_server is not None:
            if is_ipv4(dns_server):
                new_values['dns_server'] = dns_server
            else:
                errors.append(b'dns_server')
        # when N1MM mode is enabled, the fixed N1MM UDP ports cannot collide with any tcp service.
        if new_values.get('n1mm', config.get('n1mm')):
            for port in (effective_tcp_port_1, effective_tcp_port_2, effective_web_port):
                if port in (N1MM_ROTOR_BROADCAST_PORT, N1MM_BROADCAST_FROM_ROTOR_PORT):
                    errors.append(b'port %d collides with N1MM UDP port' % port)
        if not errors:
            for key, value in new_values.items():
                config[key] = value
            response = b'ok\r\n'
            http_status = HTTP_STATUS_OK
            bytes_sent = await http.send_simple_response(writer, http_status, http.CT_TEXT_TEXT, response)
        else:
            response = b'parameter(s) out of range\r\n' + b', '.join(errors) + b'\r\n'
            http_status = HTTP_STATUS_BAD_REQUEST
            bytes_sent = await http.send_simple_response(writer, http_status, http.CT_TEXT_TEXT, response)
    else:
        response = b'GET or PUT only.'
        http_status = HTTP_STATUS_BAD_REQUEST
        bytes_sent = await http.send_simple_response(writer, http_status, http.CT_TEXT_TEXT, response)
    return bytes_sent, http_status


# noinspection PyUnusedLocal
@http_server.route(b'/api/restart')
async def api_restart_callback(http, verb, args, reader, writer, request_headers=None):
    global keep_running
    if upython:
        keep_running = False
        response = b'ok\r\n'
        http_status = HTTP_STATUS_OK
        bytes_sent = await http.send_simple_response(writer, http_status, http.CT_TEXT_TEXT, response)
    else:
        http_status = HTTP_STATUS_BAD_REQUEST
        response = b'not permitted except on PICO-W'
        bytes_sent = await http.send_simple_response(writer, http_status, http.CT_APP_JSON, response)
    return bytes_sent, http_status


# rotator web actions
# noinspection PyUnusedLocal
@http_server.route(b'/api/bearing')
async def api_bearing_callback(http, verb, args, reader, writer, request_headers=None):
    requested_bearing = args.get('set')
    rotor_number = args.get('rotor', '1')
    if rotor_number == '1':
        rotator = rotator_1
        rotor_name = config.get_bytes('rotor_1_name')
    elif rotor_number == '2':
        rotator = rotator_2
        rotor_name = config.get_bytes('rotor_2_name')
    else:
        response = b'rotor_number parameter out of range\r\n'
        http_status = HTTP_STATUS_BAD_REQUEST
        bytes_sent = await http.send_simple_response(writer, http_status, http.CT_TEXT_TEXT, response)
        return bytes_sent, http_status

    if requested_bearing is not None and requested_bearing != '':
        requested_bearing = safe_int(requested_bearing)
        if 0 <= requested_bearing <= 360:
            bearing = await rotator.set_rotator_bearing(requested_bearing)
            if bearing >= 0:
                http_status = HTTP_STATUS_OK
                response = b'{\r\n  "bearing": %d,\r\n  "rotor": "%s"\r\n}\r\n' % (bearing, rotor_name)
                bytes_sent = await http.send_simple_response(writer, http_status, http.CT_APP_JSON, response)
            else:
                http_status = HTTP_STATUS_INTERNAL_SERVER_ERROR
                msg = b'set_rotator_bearing returned error: %d' % bearing
                logging.warning(msg, 'main:api_bearing_callback')
                response = b'%s\r\n' % msg
                bytes_sent = await http.send_simple_response(writer, http_status, http.CT_TEXT_TEXT, response)
        else:
            http_status = HTTP_STATUS_BAD_REQUEST
            response = b'bearing (set) parameter out of range\r\n'
            bytes_sent = await http.send_simple_response(writer, http_status, http.CT_TEXT_TEXT, response)
    else:
        bearing = await rotator.get_rotator_bearing()
        if bearing >= 0:
            response = b'{\r\n  "bearing": %d,\r\n  "rotor": "%s"\r\n}\r\n' % (bearing, rotor_name)
            http_status = HTTP_STATUS_OK
            bytes_sent = await http.send_simple_response(writer, http_status, http.CT_APP_JSON, response)
        else:
            msg = b'get_rotator_bearing returned error: %d' % bearing
            logging.warning(msg, 'main:api_bearing_callback')
            response = b'%s\r\n' % msg
            http_status = HTTP_STATUS_INTERNAL_SERVER_ERROR
            bytes_sent = await http.send_simple_response(writer, http_status, http.CT_TEXT_TEXT, response)
    return bytes_sent, http_status
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

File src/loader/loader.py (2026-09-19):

#!/bin/env python3
__author__ = 'J. B. Otterson'
__copyright__ = """
Copyright 2022, 2024, 2025, 2026 J. B. Otterson N1KDO.
Redistribution and use in source and binary forms, with or without modification, 
are permitted provided that the following conditions are met:
  1. Redistributions of source code must retain the above copyright notice, 
     this list of conditions and the following disclaimer.
  2. Redistributions in binary form must reproduce the above copyright notice, 
     this list of conditions and the following disclaimer in the documentation 
     and/or other materials provided with the distribution.
THIS SOFTWARE IS PROVIDED BY THE COPYRIGHT HOLDERS AND CONTRIBUTORS "AS IS" AND 
ANY EXPRESS OR IMPLIED WARRANTIES, INCLUDING, BUT NOT LIMITED TO, THE IMPLIED
WARRANTIES OF MERCHANTABILITY AND FITNESS FOR A PARTICULAR PURPOSE ARE DISCLAIMED.
IN NO EVENT SHALL THE COPYRIGHT HOLDER OR CONTRIBUTORS BE LIABLE FOR ANY DIRECT,
INDIRECT, INCIDENTAL, SPECIAL, EXEMPLARY, OR CONSEQUENTIAL DAMAGES (INCLUDING,
BUT NOT LIMITED TO, PROCUREMENT OF SUBSTITUTE GOODS OR SERVICES; LOSS OF USE, 
DATA, OR PROFITS; OR BUSINESS INTERRUPTION) HOWEVER CAUSED AND ON ANY THEORY OF
LIABILITY, WHETHER IN CONTRACT, STRICT LIABILITY, OR TORT (INCLUDING NEGLIGENCE 
OR OTHERWISE) ARISING IN ANY WAY OUT OF THE USE OF THIS SOFTWARE, EVEN IF ADVISED
OF THE POSSIBILITY OF SUCH DAMAGE.
"""
__version__ = '0.10.9'  # 2026-09-04

"""
Note: to edit linux forced device names, edit
/etc/udev/rules.d/99-usb-serial.rules
see: https://programmador.com/posts/2023/linux-usb-serial-device-name-binding/
see: https://k4sbc.com/consistently-name-usb-serial-ports/
"""
import argparse
import hashlib
import json
import os
import sys
import time

# need pyserial to enumerate com ports.
from serial.tools.list_ports import comports
from serial import SerialException
from pyboard import Pyboard, PyboardError

_BAUD_RATE = 115200
_BUFFER_SIZE = 2048

_WATCHDOG_PY = 'watchdog.py'

class BytesConcatenator:
    """
    this is used to collect data from pyboard functions that otherwise do not return data.
    """
    __slots__ = ('data',)

    def __init__(self):
        self.data = bytearray()

    def write_bytes(self, b):
        self.data.extend(b.replace(b"\x04", b""))

    def __str__(self):
        return self.data.decode('utf-8', errors='replace').replace('\r', '')


def get_ports_list():
    return sorted(x.device for x in comports())


# noinspection PyUnusedLocal
def put_file_progress_callback(bytes_so_far, bytes_total):
    print(f'{bytes_so_far:05d}/{bytes_total:05d} bytes sent.\r', end='', flush=True)


def put_file(filename, target, source_directory='.', src_file_name=None):
    if src_file_name is None:
        src_file_name = source_directory + filename
    else:
        src_file_name = source_directory + src_file_name

    if filename.endswith('/'):  # does it end in a slash?
        filename = filename[:-1]
        try:
            print(f'creating target directory {filename}')
            target.fs_mkdir(filename)
        except PyboardError as exc:
            if 'EEXIST' not in str(exc):
                print(f'failed to create target directory {filename}')
                return False
    else:
        try:
            os.stat(src_file_name)
        except OSError:
            print(f'cannot find source file {src_file_name}')
            return False
        try:
            print(f'sending file {src_file_name} to {filename}')
            target.fs_put(src_file_name, filename, progress_callback=put_file_progress_callback)
            print()
        except (OSError, SerialException) as exc:
            # a transient USB/serial glitch surfaces here; the local file is fine.
            # the next loader run re-sends any partially written file (sha1 mismatch).
            print(f'error sending {src_file_name}: {exc}')
            return False
    return True


def loader_bootloader(target):
    cmd = f"""import machine
machine.bootloader()
"""
    target.exec_raw_no_follow(cmd)


def loader_implementation(target):
    data = BytesConcatenator()
    cmd = f"""import sys
nm = sys.implementation.name
ver = sys.implementation.version
ver = '{{}}.{{}}.{{}}'.format(ver[0], ver[1], ver[2])
mach = sys.implementation._machine
print('{{}}|{{}}|{{}}'.format(nm, ver, mach))
"""
    target.exec_(cmd, data_consumer=data.write_bytes)
    return str(data).rstrip('\n').split('|')


def loader_ls(target, src='/'):
    files_found = []
    files_data = BytesConcatenator()
    cmd = f"""import uos
for f in uos.ilistdir('{src}'):
    print('{{}}{{}}'.format(f[0], '/' if f[1] & 0x4000 else ''))
"""
    #print(cmd)
    target.exec_(cmd, data_consumer=files_data.write_bytes)
    files = str(files_data).split('\n')
    for phile in files:
        if len(phile) > 0:
            if phile.endswith('/'):
                children = loader_ls(target, phile)
                for child in children:
                    files_found.append(f'{phile}{child}')
            files_found.append(phile)
    return files_found


def loader_reset(target):
    time.sleep(2)
    target.serial.write(b"\x04")  # control-D -- restart
    time.sleep(2)

def loader_sha1(target, file=''):
    hash_data = BytesConcatenator()
    cmd = f"""import hashlib
hasher = hashlib.sha1()
with open('{file}', 'rb') as fp:
  while True:
    buffer = fp.read(2048)
    if buffer is None or len(buffer) == 0:
      break
    hasher.update(buffer)
print(bytes.hex(hasher.digest()))
"""
    target.exec_(cmd, data_consumer=hash_data.write_bytes)
    return str(hash_data).strip()


def local_sha1(file):
    hasher = hashlib.sha1()
    with open(file, 'rb') as fp:
        while True:
            buffer = fp.read(_BUFFER_SIZE)
            if buffer is None or len(buffer) == 0:
                break
            hasher.update(buffer)
    return bytes.hex(hasher.digest())
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

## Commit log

2022-08-12 add refresh button, now has telnet client
    so far only tested with LP-Rotor
2022-08-13 change refresh UI to radio buttons
    general cleanups
2022-08-21 added hardware!
    moved some stuff around.
    [pico-w-rotator.kicad_pcb, pico-w-rotator.kicad_sch, pico-w-rotator.sch]
2022-08-24 config stuff.
    [pico-w-rotator.kicad_pcb, pico-w-rotator.kicad_sch]
2022-08-27 pcb measured, checked
    sent out to oshpark!
    [pico-w-rotator.kicad_pcb]
2022-08-28 pcb measured, checked
    schem changed, sanity
    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
    [pico-w-rotator.kicad_sch]
2022-09-05 added step file data for better 3d experience
    [pico-w-rotator.kicad_pcb]
2022-09-06 fix strings, add some api methods, etc
    [main.py]
2022-09-11 reorganized files. send IP in Morse on LED.
2022-09-11 improvements to loader, will restart device now.
2022-09-18 improvements to loader, will detect pico-w now.
    updated doc to some degree
2023-01-14 make rotor control code more portable
    by using SerialPort class.
2023-01-14 static analyzer fixes, typos.
    [loader.py, main.py]
2023-01-14 make serial connection to rotor more robust.
2023-05-27 better 404 message.
    use primitive rotor control for DCU-3
2024-01-18 add remove file support, it was missing.
    [main.py]
2024-01-20 fix upload support, remove support
    [http_server.py, main.py]
2025-07-07 reset access point mode on save
    [not_machine.py]
2026-03-17 support two rotors on the Pico-W Dual Serial card
2026-06-13 fix rotor 2 validation

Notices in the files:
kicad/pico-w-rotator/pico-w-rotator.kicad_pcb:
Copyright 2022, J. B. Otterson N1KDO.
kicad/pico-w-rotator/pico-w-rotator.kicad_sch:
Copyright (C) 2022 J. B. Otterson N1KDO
